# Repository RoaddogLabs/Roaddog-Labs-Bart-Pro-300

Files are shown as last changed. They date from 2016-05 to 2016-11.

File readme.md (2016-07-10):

## Roaddog Labs Bart Pro 300
## 
This is the Roaddog Bart Pro 300 3D printer. This machine is a larger build
based on a mashup implemented from several designs including original
designs.  

#####Bart Pro 300 uses high performance lead screws, M10 precision shaft on all axis, high temp hot end suitable to 400*C, auto bed probe (bed leveling), silcone bed heater, MIC 6 precision aluminum print surface with PEI.

### This is a pre release version
### 
The current version is a pre release.  While the machine is functional
and works well, it's still a work in progress.  There are not build docs at this point, refer to Bart Pro XL build docs at http://roaddoglabs.io/wiki/Roaddog_Labs_Bart_Pro_XL

Pull requests are welcome and encouraged.

#### Roaddog Labs Bart Pro 300 Specs ####

| Feature | Bart Pro 300 |
|---|---|
| Base and Frame | Full melamine frame, printed parts, latest design for maximum stability and print speeds |
| Build Envelope | 300 mm x 300 mm x 200 mm |
| Resolution (printable layer thickness) | low res .3 mm; normal res .2 mm; hi res .1 mm; extra hi res .06 mm |
| Filament Diameter | 1.75 |
| Max Printing Temp | 248&#176; C with E3D Lite v6; 300&#176; C with E3D full v6 with thermistor, 400&#176; C with optional thermocouple |
| Compatible Materials | With E3D v6, any printable material to 400&#176; C with E3D v6 and thermocouple.  With E3D Lite v6 more than 15 types including PLA, ABS, Laywoo-D, HIPS, carbon fiber reinforced PLA, flexible filament, conductive PLA |
| Nozzle Size | .4 mm standard, user upgradable to a variety of sizes |
| Heated Bed | silicone heater, 24 volt 250 watt|
| Print Surface |0.25" MIC-6 aluminum precision tooling plate with PEI surface| Extruder | Bart Direct Drive MK7, low profile, reduced weight and mass, optional E3D Titan or Bondtech QR extruder |
| Bed Tilt Compensation | Belt tilt compensation, also called auto bed leveling or tramming via an inductive sensor |
|Electronics | Mini Rambo configured for Bart Pro XL with Marlin firmware |
| Power Supply | 24 volts, 400 watts compact form factor |
| X Axis Motion | GT2 belt and pulley;  10 mm precision  bearings and chromed, hardened rods |
| Y Axis Motion | GT2 belt and pulley;  10 mm precision  bearings and chromed, hardened rods |
| Z Axis Motion | TR8 precision lead screw and nut; 10 mm precision bearings and chromed, hardened rods |
| Average Speeds | 100 mm/s (stock extruder, perimeters based on average tune) |
| Machine Footprint | 512 mm x 470 mm x 450 mm |
| Display/SD Card Reader | Full graphic LCD display and SD card reader for standalone operation |
| Optional Wireless and Print Server | User installed optional printing over Wifi and dedicated print server using Octoprint and a Raspberry Pi |

####License and Credits

Original designs from Roaddog Labs Ltd are released per the
Open Source Hardware Association guidelines for open source hardware at
http://www.oshwa.org/definition/.

Material specific to the Bart components and documentation that is not
derived from other sources are released under the Creative Commons
Attribution 4.0 International license.

Where applicable, the license of any derived work will be posted as
well.

The original Prusa i3 single plate files
(https://github.com/josefprusa/Prusa3) from Josef Prusa licensed under
GPL v3.

The original i3 Rework
(https://github.com/eMotion-Tech/Prusai3_EINSTEIN_Reworked) printed
parts files from eMotion-Tech are released under GPL 2.0.

The original i3 Hephestos files
(https://github.com/bq/prusa-i3-hephestos/) from bq Department of
Innovation and Robotics are licensed under Creative Commons Attribution
4.0 Sharealike International.

The Graber i3(https://github.com/sgraber/Graber) is licensed under GPL
v3.0.

The original modified i3 X idler with adjustable belt tensioner from
ramkam (http://www.thingiverse.com/thing:393870) licensed under Creative
Commons Atribution-Sharealike, no version stated.

Marlin firmware (https://github.com/MarlinFirmware/Marlin) from Erik van
der Zalm licensed under GPL, no version stated.

The original direct drive extruder for Wilson/i3
(http://www.thingiverse.com/thing:501755) from mrice licensed under
Creative Commons Attribution- Share Alike license, no version stated.

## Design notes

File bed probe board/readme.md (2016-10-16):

This is the voltage divider circuit and board layout for the Roaddog Labs Bart Pro 300.  It takes a 24 volt input and reduces the switch output to 5 volts for triggering the MCU on the printer.

This is pre release, not for production.

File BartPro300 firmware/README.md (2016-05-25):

### Roaddog Labs Bart Pro XL Firmware
### 
__Not for production use – use with caution!__

This fork is configured specifically for the Roaddog Labs Pro XL.  It's
currently based on Marlin 1.1.0-RC3 that was pushed 01 Dec, 2015.  This build is configured for a Mini Rambo controller using 360 mm x 240 mm print bed and Reprap Discount GLCD display

This build defaults to an induction probe in place of a mechanical Z end stop. The file [Configuration_mechanical_z.txt](./Bart_Pro_XL/Configuration_mechanical_z.txt) contains the settings for using a mechanical end stop in the A position.  To use this configuration rename the file to Configuration.h  and build the firmware.

The [original README.md](Orig_README.md) from the fork.

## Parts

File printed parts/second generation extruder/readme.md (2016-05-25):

Roaddog Labs Ltd Bart Pro XL 2nd Gen Extruder

This is a prototype 2nd generation extruder.  

Updates include 

provisions for the push connector in the E3D hot end

two screw JHead style mount

This is still experimental pull requests and suggestions are encouraged.

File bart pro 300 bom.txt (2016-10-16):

Bill of Materials
Roaddog Labs Ltd Bart Pro 300
file released under Creative Commons
Attribution 4.0 International license.

Frame

5 x 24" x18" 1/4" melamine, two sides laminated

Rods

2 x TR8 x 300 mm lead screws and nuts (recommend lead screws integrated with Z motors similar to https://www.pololu.com/product/2268)

2 x M10 x 320 Z axis precision rod (for 180 mm vertical build envelope)

2 x M10 x 400 mm X axis precision rod

2 x M10 x 511 mm Y axis precision rod

Bearings

12 x LM10UU linear bearings
2 x 624ZZ bearings
1 x 608ZZ bearings

Printed Parts

4 x Y clips
1 x Y motor bracket
8 x Y bearing mounts (each mount is two pieces)
1 x Y belt idler
1 x Y bed belt bracket

1 x X carriage
1 x x endstop block
1 x X end motor
1 x X end idler
1 x X idler

1 x extruder body 
1 x extruder idler
1 x hot end mounting clip
1 x fan duct
1 x bed probe mount

1 x z endstop bracket/ rod guide base
1 x z rod guide base

Misc Hardware

1 x M7 hobbed drive gear, filament drive gear
2 x GT2 pulley, 20 teeth, 5 mm diameter mounting hole
2 meters GT2 belt

4 x rubber feet

2 x rod couplers (not needed if lead screws are integrated with motors)

1 x 300 mm x 300 mm x .25 mm MIC-6 aluminum build plate

4 bed spacers (get final specs)
2 extruder springs (get final specs)

Fasteners 

50 x 6-32 square nut, frame
50 x 6-32 x 5/8" pan head machine screws, frame

20 x  M3 x 10 mm shcs, motor mounts, endstop screws
25 x  M3 x 12 mm shcs, motor/Z endstop bracket mounting, feet mounting
10 x  M3 x 14 mm shcs,
05 x  M3 x 16 mm shcs,
08 x  M3 x 25 mm shcs,
06 x  M3 x 30 mm shcs, 
02 x  M3 x 35 mm shcs,
02 x  M3 x 50 mm shcs,

55 x  M3 washer
30 x  M3 hex nut
12 x  M3 nyloc nut

07 x  M4 x 20 shcs extruder mount, extruder idler
01 x  M4 x 30 shcs Y idler bearing

06 x  M4 hex nut
10 x  M4 flat washer
03 x  M4 nyloc nut

01 x  M8 x 30 mm shcs
01 x  M8 nyloc nut
06 x  M8 flat washer

Electronics

1 x Mini Rambo control board

1 x 40x40x10 24 volt axial fan

5 x NEMA 17 stepper motors, recommend 76 oz/in holding torque

1 x 400 watt, 24 volt PSU

1 x 300 mm x 300 mm 24 volt, 250 watt silicone heating pad with 100k ohm thermistor

1 x inductive probe, LJ12A3-4-Z/BX w/voltage divider for signal return

1 x E3D v6 hot end kit, 24 volt

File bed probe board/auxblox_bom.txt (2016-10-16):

Partlist exported from /Users/dave/Documents/eagle/auxblox/auxblox.sch at 10/16/16 1:37 PM

Part Value   Device                              Package Description               VALUE  
CN1  3p-2.54 DIP-BLACK-MALE-HEADER-VERT(3P-2.54) H3-2.54 320020079                 3p-2.54
CN2  3p-2.54 DIP-BLACK-MALE-HEADER-VERT(3P-2.54) H3-2.54 320020079                 3p-2.54
R1   1k      R-EU_R0805                          R0805   RESISTOR, European symbol        
R2   3.3K    R-EU_R0805                          R0805   RESISTOR, European symbol

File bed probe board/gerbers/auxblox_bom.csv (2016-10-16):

CN1,CN2 | S1011EC-40-ND | 2
R1 | 985-1300-1-ND | 1
R2 | 985-1311-1-ND | 1

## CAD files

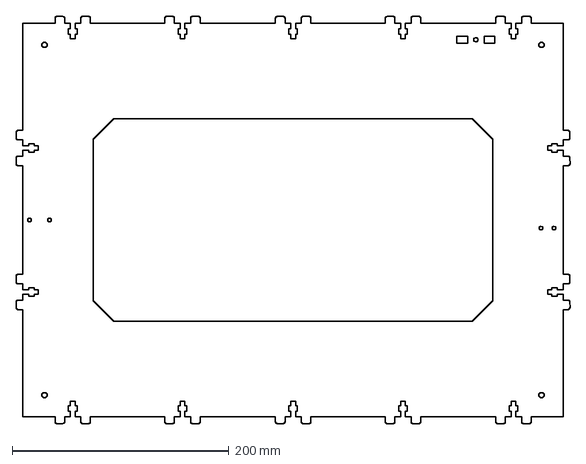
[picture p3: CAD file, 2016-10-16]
frame/bart pro 300 base new y idler.dxf
511.3 x 376.0 mm

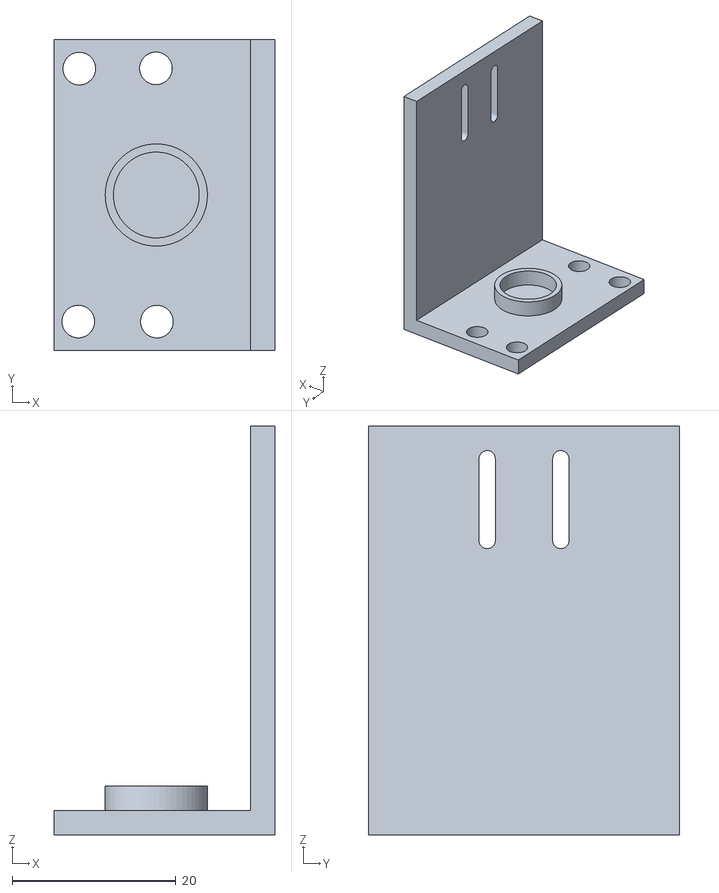
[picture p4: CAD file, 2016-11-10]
printed parts/bart 300 z endstop bracket.stl
27.0 x 38.0 x 50.0

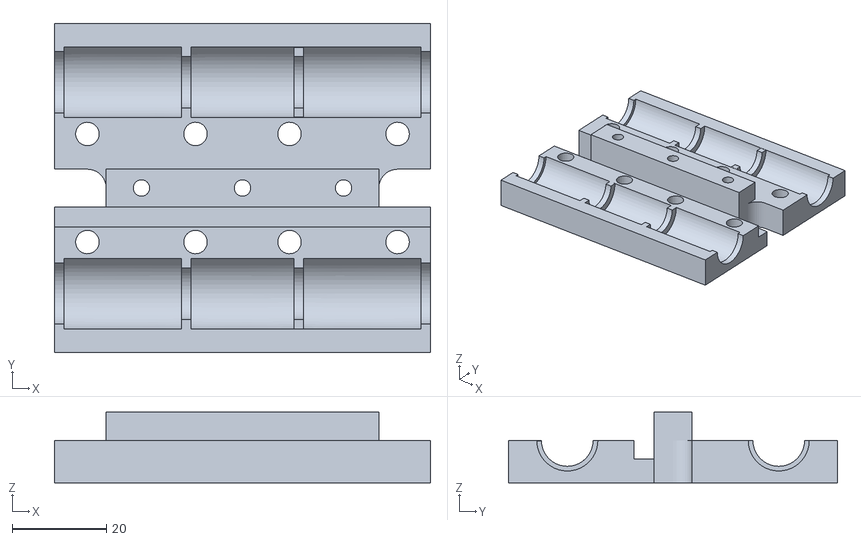
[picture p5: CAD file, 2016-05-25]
printed parts/dual extruder/bart xl dual extruder x carriage either bearings rear.stl
80.0 x 70.0 x 15.0

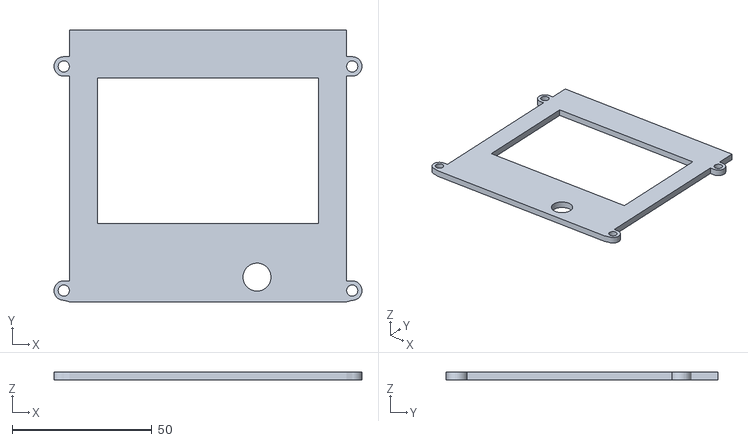
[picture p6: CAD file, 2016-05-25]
printed parts/glcd case/bart pro xl glcd case face.stl
110.0 x 97.0 x 3.00

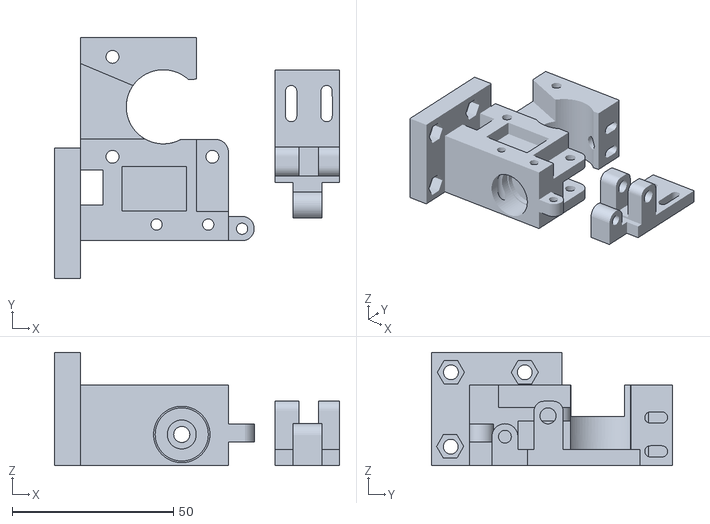
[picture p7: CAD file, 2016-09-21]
printed parts/second generation extruder/bart pro xl 2nd gen extruder.stl
88.5 x 74.8 x 35.2

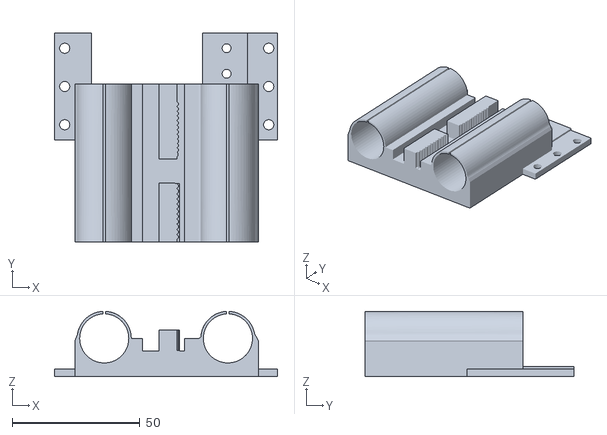
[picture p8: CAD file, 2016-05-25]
printed parts/titan x carriage-bracket/bart pro xl titan x carriage.stl
87.4 x 82.0 x 25.6

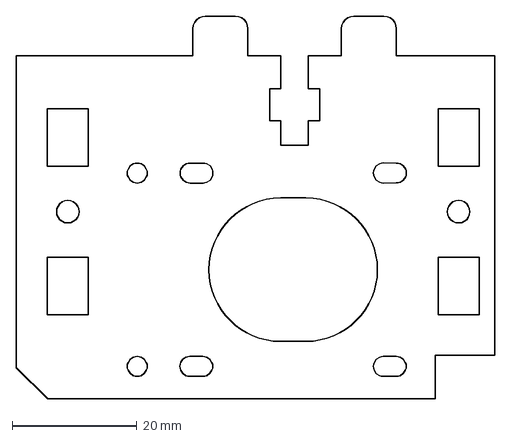
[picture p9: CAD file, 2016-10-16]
frame/bart pro 300 z motor mount adjustable.dxf
76.7 x 61.3 mm

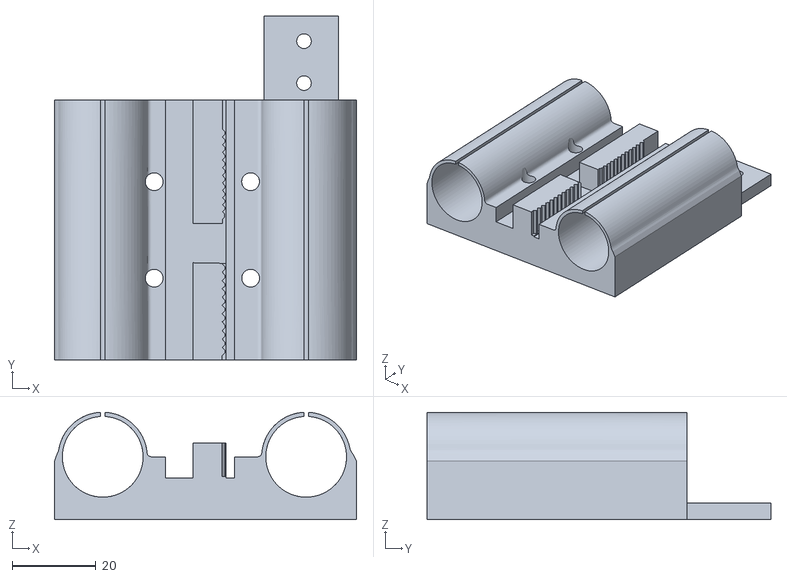
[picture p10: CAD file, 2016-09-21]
printed parts/bart 300 x carriage RC.stl
72.0 x 82.0 x 25.6

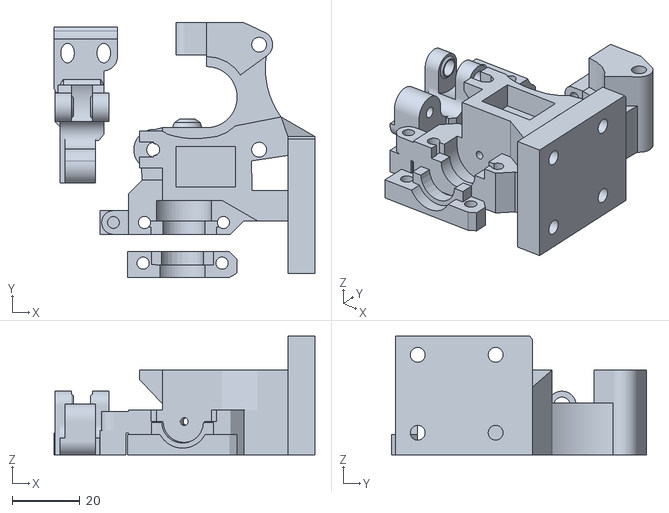
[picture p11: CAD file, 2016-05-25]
printed parts/dual extruder/extruder motor on right.stl
77.1 x 75.2 x 35.0

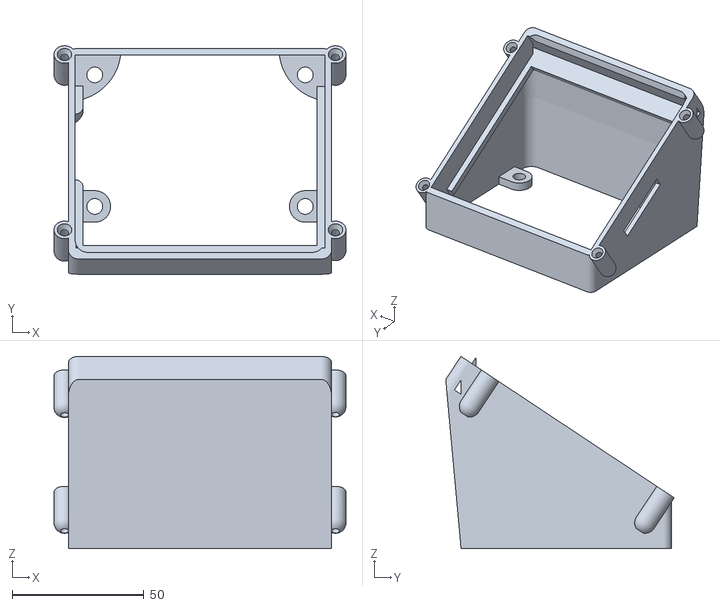
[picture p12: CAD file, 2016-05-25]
printed parts/glcd case/bart pro xl glcd case base.stl
111.0 x 86.9 x 73.1

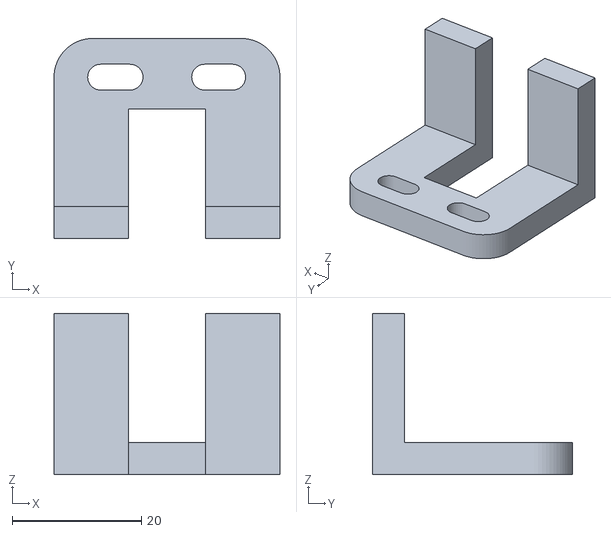
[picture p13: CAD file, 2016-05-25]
printed parts/second generation extruder/bart pro xl 2nd gen probe mount.stl
35.0 x 31.0 x 25.0

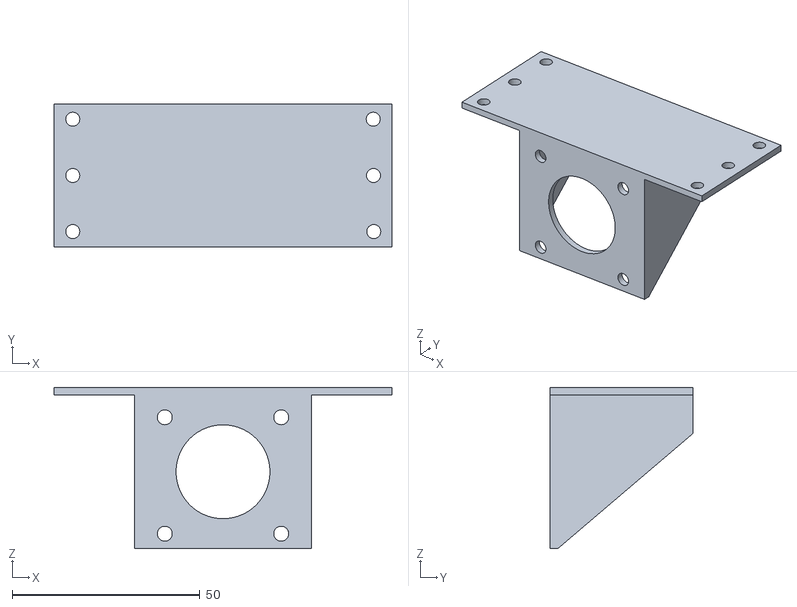
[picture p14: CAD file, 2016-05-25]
printed parts/titan x carriage-bracket/bart pro xl titan bracket.stl
90.0 x 38.0 x 43.0

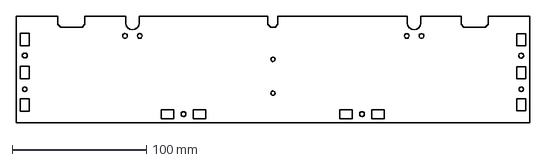
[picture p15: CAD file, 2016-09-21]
frame/bart pro 300 end front new Y idler.dxf
382.0 x 79.1 mm

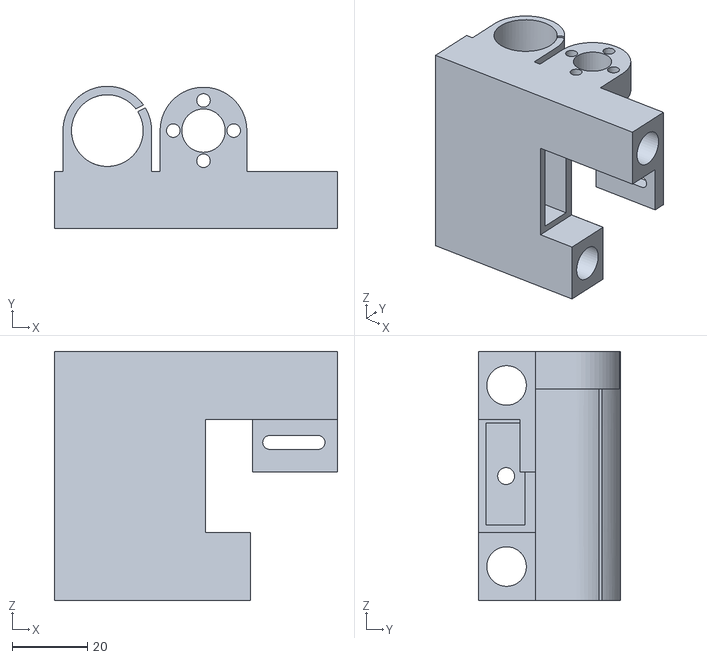
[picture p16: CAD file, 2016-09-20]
printed parts/bart 300 X idler end RC.stl
75.0 x 37.7 x 66.0

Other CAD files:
printed parts/dual extruder/bart xl dual extruder x carriage lm8uu front.stl
frame/bart pro 300 side.dxf
printed parts/bart pro 300 y belt idler RC.stl
printed parts/dual extruder/bart xl dual extruder x carriage igus bearings front.stl
BartPro300 firmware DEPRECATED/Documentation/Logo/Marlin Logo_old.dxf
frame/bart pro 300 end rear.dxf
frame/bart pro 300 print bed.dxf
frame/bart pro 300 y endstop bracket.dxf
frame/bart pro 300 z frame.dxf
frame/bart pro 300 z motor support.dxf
frame/bart pro 300 z top rod stop.dxf
frame/bart pro 300 z top.dxf
printed parts/bart 300 Y bearing mounts.stl
printed parts/bart 300 bed probe bracket.stl
printed parts/bart 300 belt anchor.stl
printed parts/bart 300 extruder fan duct.stl
printed parts/bart 300 extruder motor on left.stl
printed parts/bart 300 single bearing x carriage.stl
printed parts/bart 300 x endstop block.stl
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

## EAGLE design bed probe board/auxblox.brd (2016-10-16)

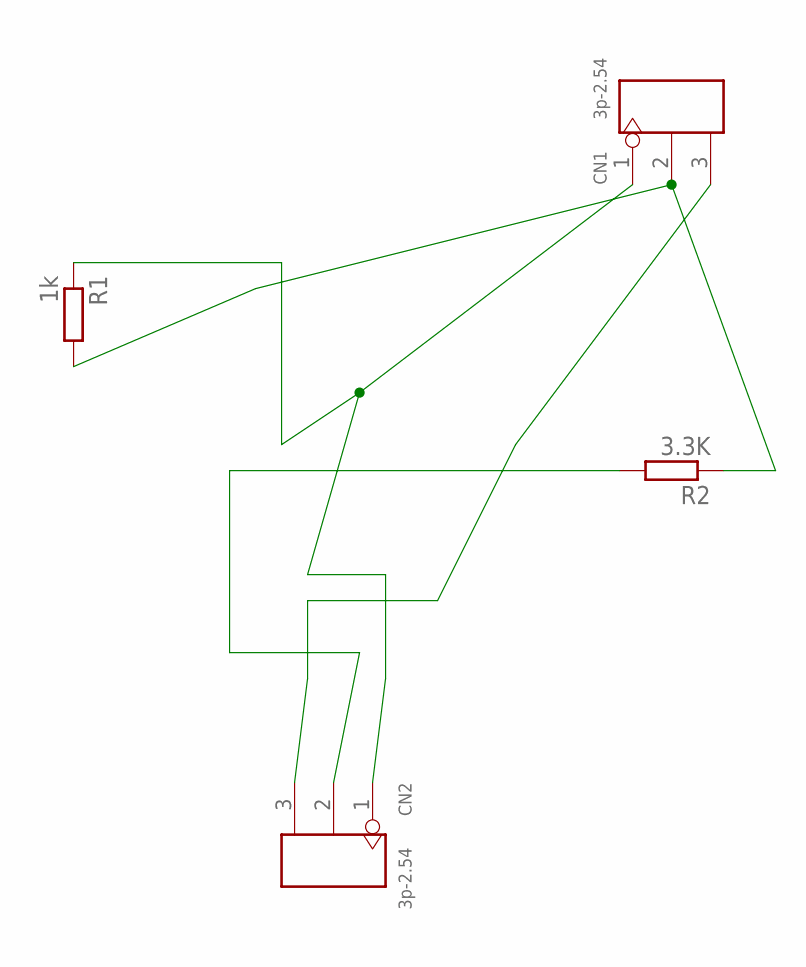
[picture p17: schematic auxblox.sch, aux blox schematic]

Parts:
CN1, CN2: 3p-2.54; H3-2.54
R1: 1k; R0805
R2: 3.3K; R0805

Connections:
unnamed: CN1.3, CN2.3
unnamed: CN2.2, R2.2
unnamed: CN1.1, CN2.1, R1.1
unnamed: CN1.2, R1.2, R2.1

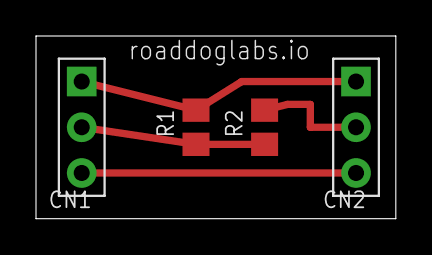
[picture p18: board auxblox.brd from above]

Board: 2 copper layers, 20.0 x 10.1 mm, 4 parts (0 on the bottom side), 4 nets.

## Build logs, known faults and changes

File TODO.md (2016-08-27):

##To Do list for outstanding issues/feature enhancements/ etc

- [x] validate Titan single bearing per rod mounts

     - [x] print titan mount prototypes
     - [ ] test titan mounts

- [ ] print and test m8 y idler parts

- [ ] fix fix bed temp monitor
     - [x] removed trigger
     - [ ] fully monitor issue by changing temp check frequency

- [ ] print and validate latest 2nd gen extruder

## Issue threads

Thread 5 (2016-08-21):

widen y motor mount mount points

RoaddogLabs, 2016-08-21:
bigger footprint for y motor mount
prototype abs or petg for heat resistance

RoaddogLabs, 2016-08-22:
mod to part, print and test as per #9

Closed 2016-08-22.

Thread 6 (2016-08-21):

validate y axis belt alignment

RoaddogLabs, 2016-08-21:

RoaddogLabs, 2016-08-27:
needs to have y belt idler modified for 628zz bearing and m8 screw (m8 x 35 shcs w/ washer and locknut)

Closed 2016-09-21.

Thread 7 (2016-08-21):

tune motor current digipot settings

RoaddogLabs, 2016-08-21:
tune the motor current to address motor heat issues

RoaddogLabs, 2016-08-22:
set to 100

heat issues are less, more testing required

Closed 2016-08-22.

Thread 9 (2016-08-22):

reference #5 print new part in abs

RoaddogLabs, 2016-08-22:
moved bottom screw hole for more stability to fix #5
print in abs for more heat

RoaddogLabs, 2016-08-27:
needs to print and test, design validated

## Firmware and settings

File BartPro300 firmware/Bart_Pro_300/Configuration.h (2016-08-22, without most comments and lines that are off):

#define CONFIGURATION_H
#include "boards.h"
#include "macros.h"
#if ENABLED(USE_AUTOMATIC_VERSIONING)
  #include "_Version.h"
#else
  #include "Default_Version.h"
#endif
#define STRING_CONFIG_H_AUTHOR "(RoaddogLabsLtd, BartProXL)" // Who made the changes.
#define SHOW_BOOTSCREEN
#define STRING_SPLASH_LINE1 SHORT_BUILD_VERSION // will be shown during bootup in line 1
#define SERIAL_PORT 0
#define BAUDRATE 250000
  #define MOTHERBOARD BOARD_MINIRAMBO
#define CUSTOM_MACHINE_NAME "Bart Pro XL"
#define EXTRUDERS 1
#define POWER_SUPPLY 1
#define TEMP_SENSOR_0 5
#define TEMP_SENSOR_1 0
#define TEMP_SENSOR_2 0
#define TEMP_SENSOR_3 0
#define TEMP_SENSOR_BED 60
#define MAX_REDUNDANT_TEMP_SENSOR_DIFF 10
#define TEMP_RESIDENCY_TIME 10  // (seconds)
#define TEMP_HYSTERESIS 3       // (degC) range of +/- temperatures considered "close" to the target one
#define TEMP_WINDOW     1       // (degC) Window around target to start the residency timer x degC early.
#define HEATER_0_MINTEMP 5
#define HEATER_1_MINTEMP 5
#define HEATER_2_MINTEMP 5
#define HEATER_3_MINTEMP 5
#define BED_MINTEMP 5
#define HEATER_0_MAXTEMP 300
#define HEATER_1_MAXTEMP 300
#define HEATER_2_MAXTEMP 275
#define HEATER_3_MAXTEMP 275
#define BED_MAXTEMP 150
#define PIDTEMP
#define BANG_MAX 255 // limits current to nozzle while in bang-bang mode; 255=full current
#define PID_MAX BANG_MAX // limits current to nozzle while PID is active (see PID_FUNCTIONAL_RANGE below); 255=full current
  #define PID_FUNCTIONAL_RANGE 10 // If the temperature difference between the target temperature and the actual temperature
  #define PID_INTEGRAL_DRIVE_MAX PID_MAX  //limit for the integral term
  #define K1 0.95 //smoothing factor within the PID
	#define  DEFAULT_Kp 15.8
    #define  DEFAULT_Ki 1.08
    #define  DEFAULT_Kd 120
#define MAX_BED_POWER 255 // limits duty cycle to bed; 255=full current
#define PREVENT_DANGEROUS_EXTRUDE
#define PREVENT_LENGTHY_EXTRUDE
#define EXTRUDE_MINTEMP 170
#define EXTRUDE_MAXLENGTH (X_MAX_LENGTH+Y_MAX_LENGTH) //prevent extrusion of very large distances.
  #define ENDSTOPPULLUP_XMAX
  #define ENDSTOPPULLUP_YMAX
  #define ENDSTOPPULLUP_ZMAX
  #define ENDSTOPPULLUP_XMIN
  #define ENDSTOPPULLUP_YMIN
const bool X_MIN_ENDSTOP_INVERTING = true; // set to true to invert the logic of the endstop.
const bool Y_MIN_ENDSTOP_INVERTING = true; // set to true to invert the logic of the endstop.
const bool Z_MIN_ENDSTOP_INVERTING = false; // set to true to invert the logic of the endstop.
const bool X_MAX_ENDSTOP_INVERTING = true; // set to true to invert the logic of the endstop.
const bool Y_MAX_ENDSTOP_INVERTING = true; // set to true to invert the logic of the endstop.
const bool Z_MAX_ENDSTOP_INVERTING = true; // set to true to invert the logic of the endstop.
const bool Z_MIN_PROBE_ENDSTOP_INVERTING = false; // set to true to invert the logic of the endstop.
#define X_ENABLE_ON 0
#define Y_ENABLE_ON 0
#define Z_ENABLE_ON 0
#define E_ENABLE_ON 0 // For all extruders
#define DISABLE_X false
#define DISABLE_Y false
#define DISABLE_Z false
#define DISABLE_E false // For all extruders
#define DISABLE_INACTIVE_EXTRUDER true //disable only inactive extruders and keep active extruder enabled
#define INVERT_X_DIR true    // Bart set to true
#define INVERT_Y_DIR false    // Bart set to false
#define INVERT_Z_DIR true     // Bart set to true
#define INVERT_E0_DIR false   // Bart MK7 direct drive motor on left set to false, motor on right set to true, Gregs Wades set to false
#define INVERT_E1_DIR false    // Bart MK7 direct drive motor on left set to false, motor on right set to true
#define INVERT_E2_DIR false   // not used for Bart
#define X_HOME_DIR 1
#define Y_HOME_DIR -1
#define Z_HOME_DIR -1
#define min_software_endstops true // If true, axis won't move to coordinates less than HOME_POS.
#define max_software_endstops true  // If true, axis won't move to coordinates greater than the defined lengths below.
#define X_MIN_POS 0
#define Y_MIN_POS 0
#define Z_MIN_POS 0
#define X_MAX_POS 300
#define Y_MAX_POS 300
#define Z_MAX_POS 200
#define DEBUG_LEVELING_FEATURE
#define Z_MIN_PROBE_REPEATABILITY_TEST  // If not commented out, Z-Probe Repeatability test will be included if Auto Bed Leveling is Enabled.
#define HOMING_FEEDRATE {50*60, 50*60, 4*60, 0}  // set the homing speeds (mm/min)
#define DEFAULT_AXIS_STEPS_PER_UNIT   {80,80,400,456}  // default steps per unit for T8 lead screw Bart Pro XL E3D Titan direct drive extruder
#define DEFAULT_MAX_FEEDRATE          {300, 300, 2, 25}    // (mm/sec)
#define DEFAULT_MAX_ACCELERATION      {3000,3000,10,10000}    // X, Y, Z, E maximum start speed for accelerated moves. E default values are good for Skeinforge 40+, for older versions raise them a lot.
#define DEFAULT_ACCELERATION          3000    // X, Y, Z and E acceleration in mm/s^2 for printing moves
#define DEFAULT_RETRACT_ACCELERATION  3000    // E acceleration in mm/s^2 for retracts
#define DEFAULT_TRAVEL_ACCELERATION   3000    // X, Y, Z acceleration in mm/s^2 for travel (non printing) moves
#define DEFAULT_XYJERK                6.0    // (mm/sec)  //set from Bart default =20
#define DEFAULT_ZJERK                 0.4     // (mm/sec)
#define DEFAULT_EJERK                 5.0    // (mm/sec)
#define CUSTOM_M_CODES
#define PLA_PREHEAT_HOTEND_TEMP 200
#define PLA_PREHEAT_HPB_TEMP 50
#define PLA_PREHEAT_FAN_SPEED 0   // Insert Value between 0 and 255
#define ABS_PREHEAT_HOTEND_TEMP 230
#define ABS_PREHEAT_HPB_TEMP 100
#define ABS_PREHEAT_FAN_SPEED 0   // Insert Value between 0 and 255
#define LANGUAGE_INCLUDE GENERATE_LANGUAGE_INCLUDE(en)
  #define DISPLAY_CHARSET_HD44780_JAPAN        // this is the most common hardware
#define ULTRA_LCD  //general LCD support, also 16x2
#define SDSUPPORT // Enable SD Card Support in Hardware Console
#define REPRAP_DISCOUNT_FULL_GRAPHIC_SMART_CONTROLLER
#define SOFT_PWM_SCALE 0
#define FILAMENT_SENSOR_EXTRUDER_NUM 0   //The number of the extruder that has the filament sensor (0,1,2)
#define MEASUREMENT_DELAY_CM        14   //measurement delay in cm.  This is the distance from filament sensor to middle of barrel
#define DEFAULT_NOMINAL_FILAMENT_DIA 3.00  //Enter the diameter (in mm) of the filament generally used (3.0 mm or 1.75 mm) - this is then used in the slicer software.  Used for sensor reading validation
#define MEASURED_UPPER_LIMIT         3.30  //upper limit factor used for sensor reading validation in mm
#define MEASURED_LOWER_LIMIT         1.90  //lower limit factor for sensor reading validation in mm
#define MAX_MEASUREMENT_DELAY       20     //delay buffer size in bytes (1 byte = 1cm)- limits maximum measurement delay allowable (must be larger than MEASUREMENT_DELAY_CM  and lower number saves RAM)
#define DEFAULT_MEASURED_FILAMENT_DIA  DEFAULT_NOMINAL_FILAMENT_DIA  //set measured to nominal initially
#include "Configuration_adv.h"
#include "thermistortables.h"

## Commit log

2016-05-25 frame updates
    add main plate and top, convert rear end plate to dxf
    [bart pro 300 end rear.dxf, bart pro 300 z frame.dxf, bart pro 300 z top.dxf]
2016-07-25 update print bed mounting
    [bart pro 300 print bed.dxf]
2016-07-25 update belt anchor mount holes
    [bart pro 300 belt anchor v2.f3d, bart pro 300 belt anchor.f3d, bart pro 300 belt anchor.stl]
2016-08-22 printed parts update and cleanup
    update various printed parts
    move m10 parts to main folder
    rename parts for consistency
    [bart 300 Y bearing mounts.stl, bart 300 bed probe bracket.stl, bart 300 belt anchor.stl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]
2016-08-22 update firmware, move to RC7
    final config update prior to move to RC7 firmware
    [Configuration.h]
2016-08-22 deprecate this version for RC7
    RC7 at https://github.com/RoaddogLabs/Marlin
    [Configuration.h, Configuration_adv.h, Configuration_mechanical_z.txt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]
2016-08-22 update bom
2016-08-23 parts cleanup, file naming
    [bart 300 bed bearing mount.f3d, bart 300 bed probe bracket.f3d, bart 300 belt anchor.f3d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]
2016-08-27 update to larger x belt idler
    [bart 300 x idler.f3d, bart 300 y motor mount wider mount.stl]
2016-09-19 misc parts update
    [bart 300 bottom z rod bracket.f3d, bart 300 z rod bracket.stl, bart pro 300 y belt idler v4.f3d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]
2016-09-20 update x idler end endstop mount
    [bart 300 X idler end v13.f3d, bart 300 x idler end.stl]
2016-09-20 update current x idler end source
    [bart 300 x idler end v11.f3d]
2016-09-21 update x carriage, x belt idler, 2nd gen extruder
    [bart 300 x belt idler.stl, bart 300 x carriage.stl, bart pro xl 2nd gen extruder idler.stl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]
2016-09-21 updated frame front
    [bart pro 300 end front new Y idler.dxf]
2016-09-21 add frame side to repo
    [bart pro 300 side.dxf]
2016-10-16 up date z motor mount to adjustable
    [bart pro 300 z motor mount adjustable.dxf]
2016-10-16 update printed parts for RC
    [bart 300 X idler end RC.stl, bart 300 x carriage RC.stl, bart 300 x motor end RC.stl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]
2016-10-16 update bed probe board
    [auxblox.brd, auxblox.sch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]
2016-10-16 add BOM for probe board
    update mom for larger components
2016-10-16 new base for new y idler
    [bart pro 300 base new y idler.dxf]
2016-10-16 clean up older file versions
    [bart pro 300 base.dxf, bart pro 300 end front.dxf]
2016-11-10 update z end stop bracket
    [bart 300 z endstop bracket.stl]
